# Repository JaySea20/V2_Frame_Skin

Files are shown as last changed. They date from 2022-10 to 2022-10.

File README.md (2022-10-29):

# V2_Frame_Skin  
Rounded Extrusion Covers to give your Voron 2.4 a sleek, smooth asthetic.  
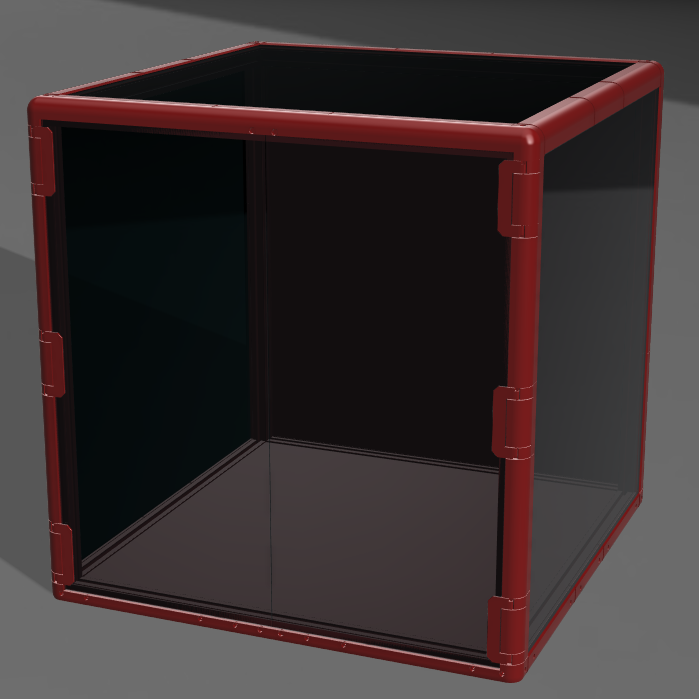
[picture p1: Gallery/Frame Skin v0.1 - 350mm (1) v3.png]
  
  
I Love my Voron 2.4r2. It sets a new bar for what a 3D Printer should be capable of.  
But, Ive never really liked the look of the Aluminum Extrusions that have been so commonly utilized for DIY CNC machines, printers, etc...  
And the only alternative seems to be the overly bulky quarter round extrusions like used in the DOOM project.  
So, I started from scratch with a few goals:  
 1 - As Low Profile as Possible. I have a 350 v2. I dont need that sucker being any bigger than it has to be ( or already is )  
 2 - Get rid of ALL sharp edges/corners/protrusions. Soon after I completed my build, I was walking past my newly built additive manufacturing beast of a printer and veered a bit too close. A corner caught just above my hip and left a nasty cut. Don't want to do that again.  
 3 - Must work with existing build. I didnt want to have to start swapping out extrusions, acrylic panels, or even have to disasemble anything gantry or below.  
 4 - As few visible screw heads as possible without overly complicating the installation.  
 5 - And, of course, it has to be a "printable" mod. ( All parts are printable besides a few screws and t-nuts. )  
   
 PLEASE NOTE:  
 These parts are not necessarily easy to print.  
 I found that printing them standing vertically worked the best for me. YMMV  
 Tolerances are tight. So calibration needs to be spot on. I tried printing some of them on my Ender3 and found its kinematics to be too sloppy.  
 Several of the parts will need supports. ( Hinge Body, Upper Corners, etc )  
   
 BOM  
| Part  | Quantity |
| --- | --- |
| Heat Set Inserts  | 4 |
| 6x3 Magnets | 8 |
| M3 Hammerhead T-Nuts| 32 |
| M3x12 SHCS | 4 |
| M3x8 SHCS | 32 |
| M2x16 SHCS | 12 |  
  
-Jay

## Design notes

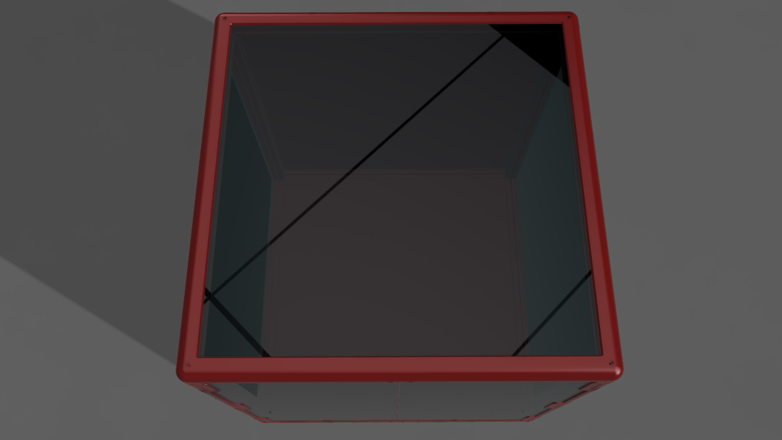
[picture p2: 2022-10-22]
Gallery/Frame Skin v0.1 - 350mm Top_view_front_profile.png

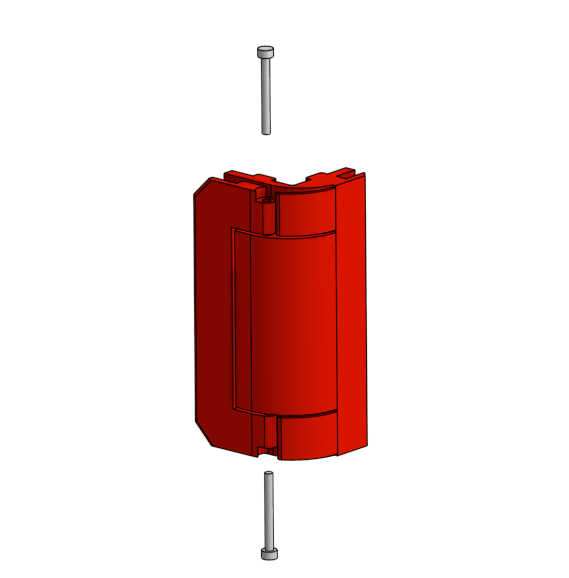
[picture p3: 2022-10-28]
Gallery/Hinge_Pins.png

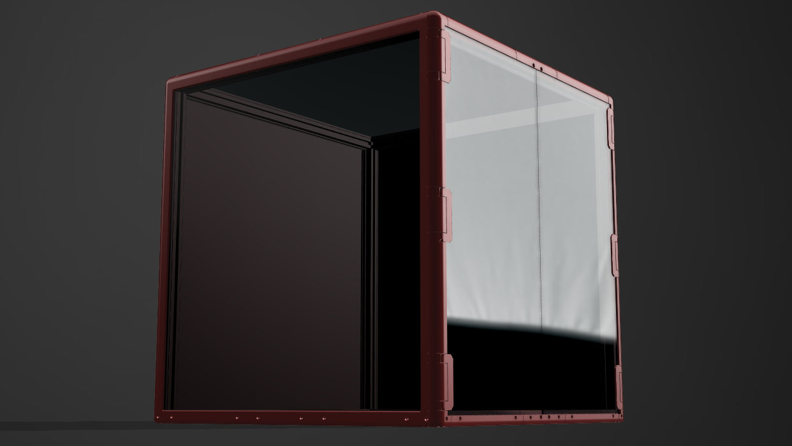
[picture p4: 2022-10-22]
Gallery/Frame Skin v0.1 - 350mm - Left_full_upwards.png

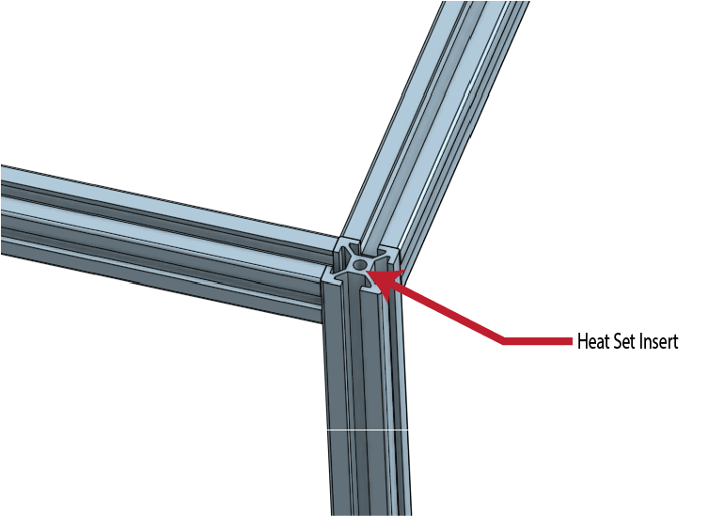
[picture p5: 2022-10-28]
Gallery/HeatSetInsert-01.png

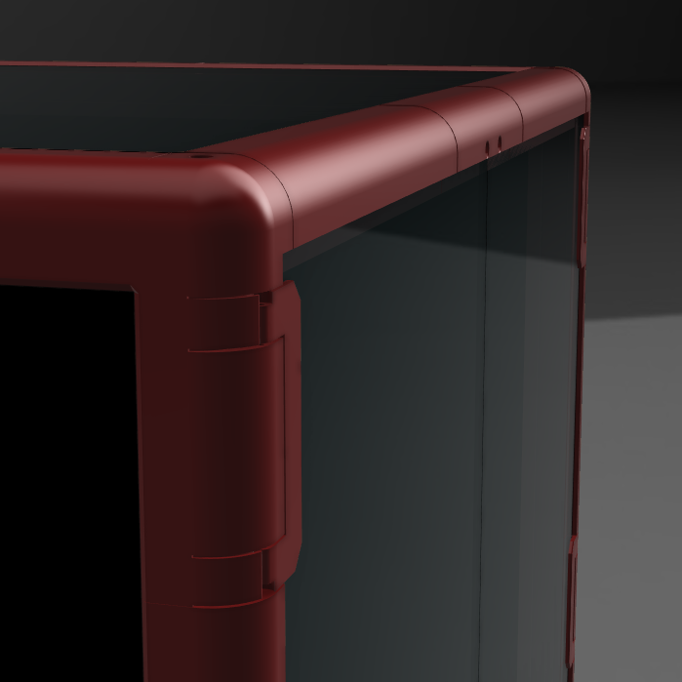
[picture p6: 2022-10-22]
Gallery/Frame Skin v0.1 - 350mm Zoomed_top_corner.png

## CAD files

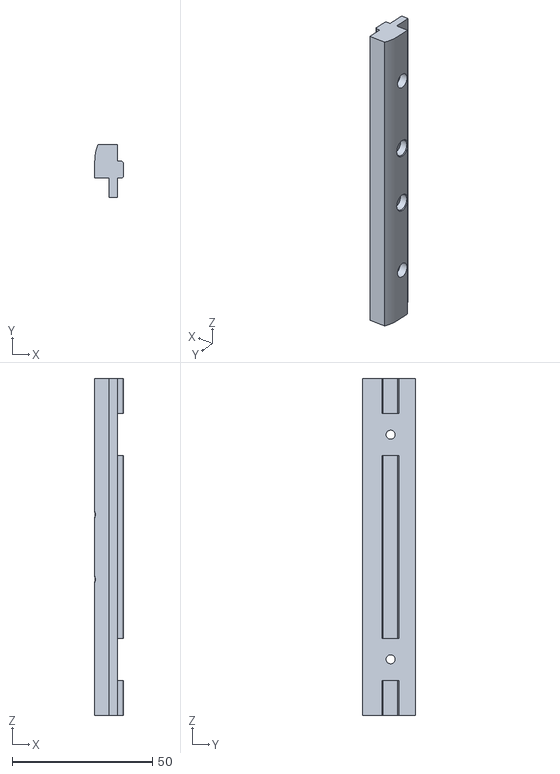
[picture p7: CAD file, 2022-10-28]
STL/350mm/Bottom_Front_Center_350_x1.stl
10.1 x 18.9 x 120.0

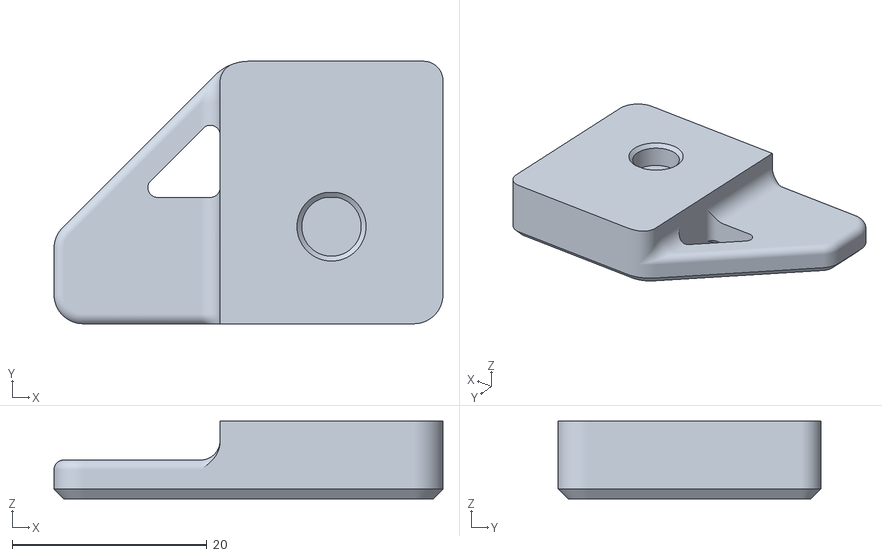
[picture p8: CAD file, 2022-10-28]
STL/Door_Handle_B_x2.stl
40.0 x 27.0 x 8.00

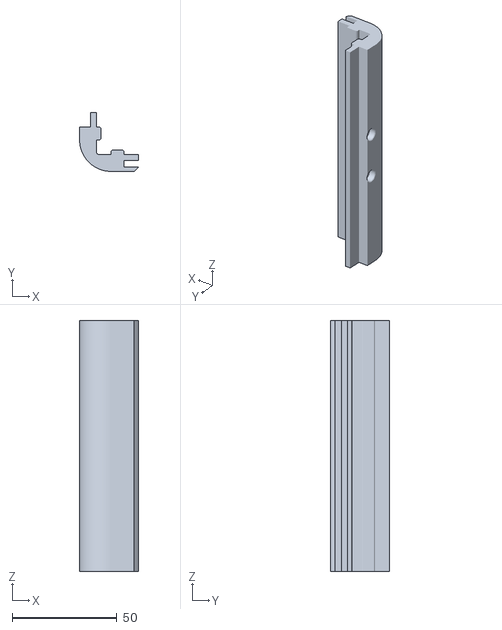
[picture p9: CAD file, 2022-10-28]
STL/350mm/Top_Front_Center_350_x1.stl
28.1 x 28.1 x 120.0

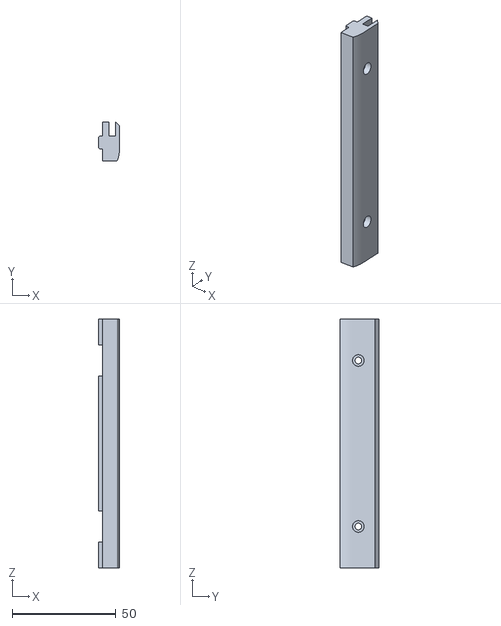
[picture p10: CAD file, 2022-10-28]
STL/350mm/Lower_120mm_350_x3.stl
10.2 x 18.9 x 120.0

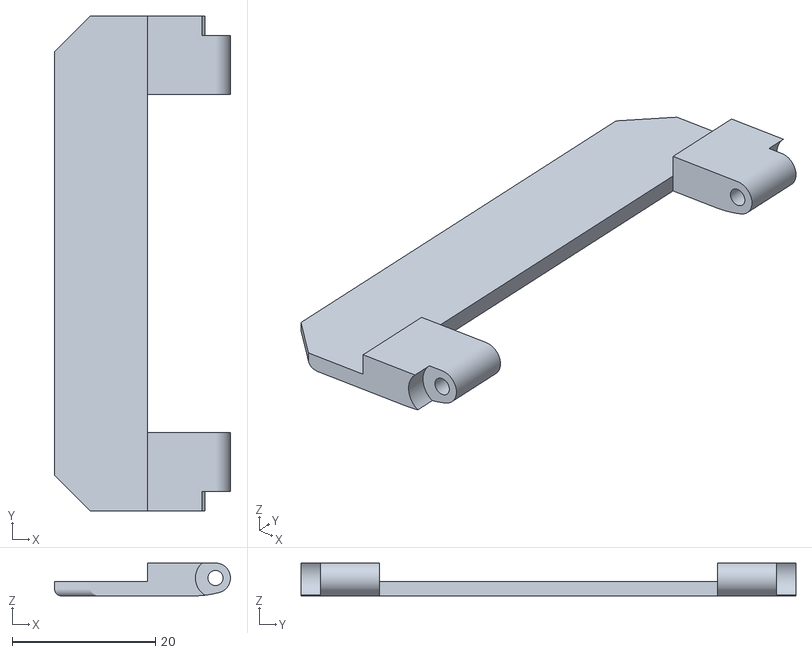
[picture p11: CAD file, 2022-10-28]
STL/Hinge_Arm_x6.stl
24.5 x 69.0 x 4.60

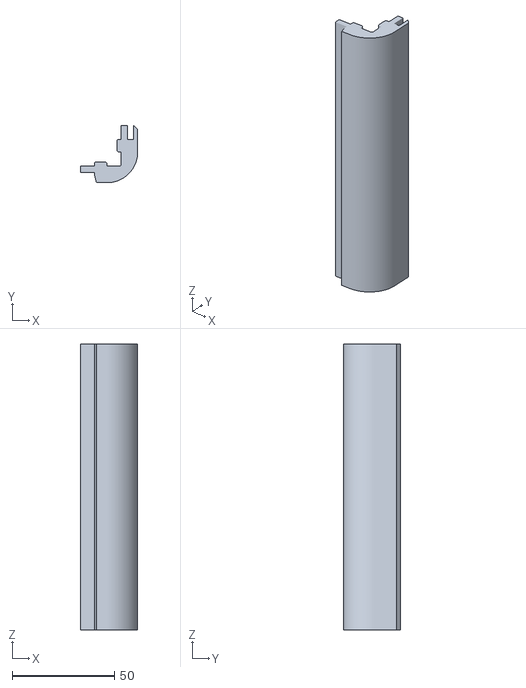
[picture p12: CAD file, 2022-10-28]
STL/350mm/Hinge_Spacer_140mm_350_x4.stl
28.1 x 28.1 x 140.0

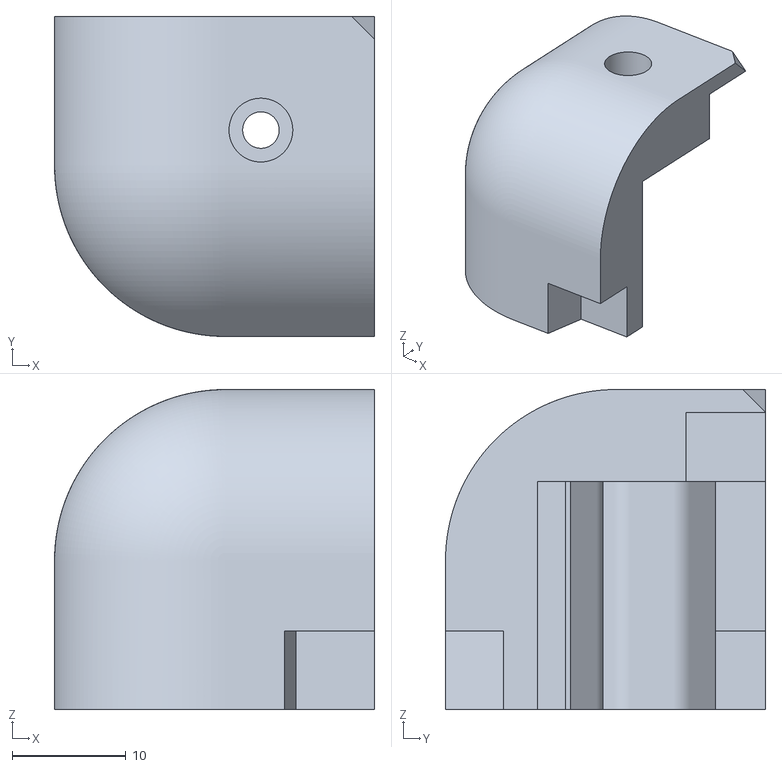
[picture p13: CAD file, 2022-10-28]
STL/Top_Front_Corner_L_x1.stl
28.1 x 28.1 x 28.1

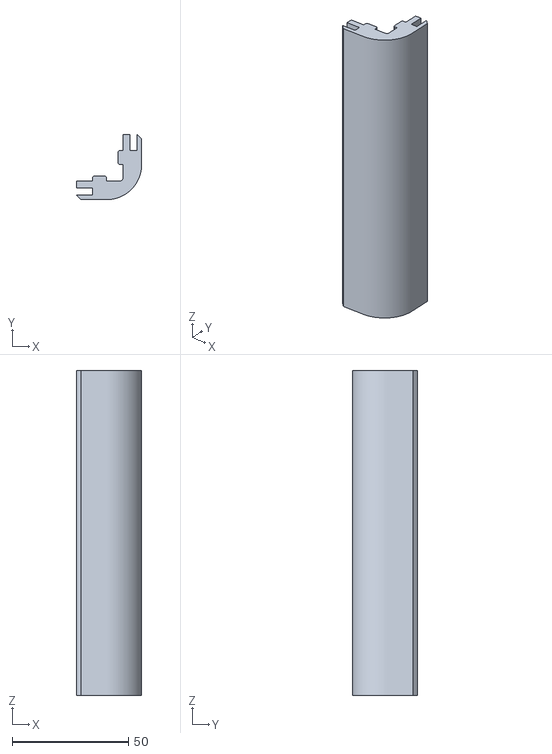
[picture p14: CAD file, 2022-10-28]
STL/350mm/Generic_140mm_350_x2.stl
28.1 x 28.1 x 140.0

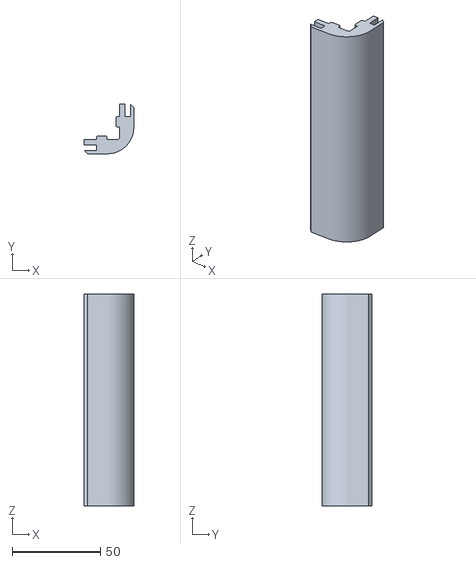
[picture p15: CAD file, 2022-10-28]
STL/350mm/Upper_120mm_350_x3.stl
28.1 x 28.1 x 120.0

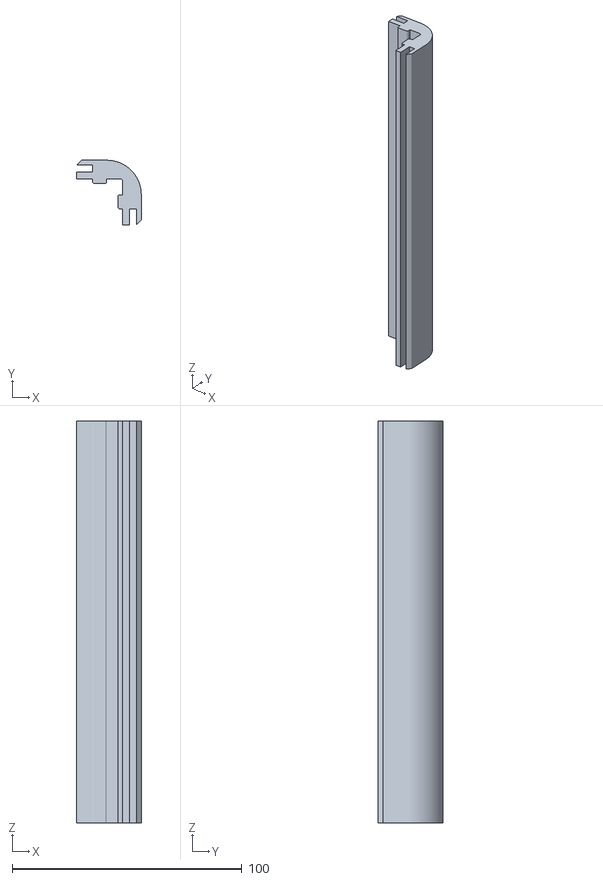
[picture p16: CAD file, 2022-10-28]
STL/Generic_175mm_x10.stl
28.1 x 28.1 x 175.0

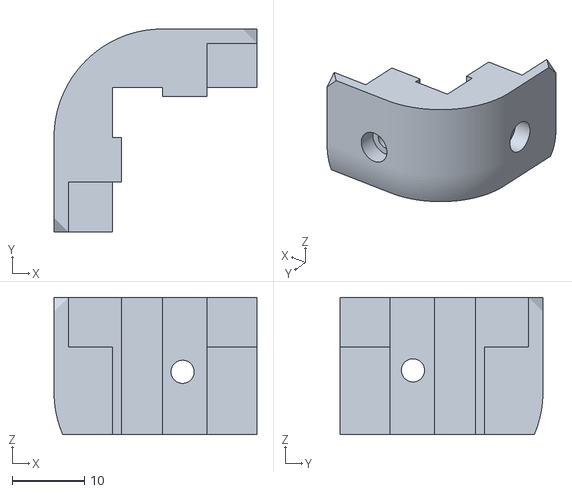
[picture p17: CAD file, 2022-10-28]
STL/Bottom_Back_Corner_x2.stl
28.1 x 28.1 x 19.0

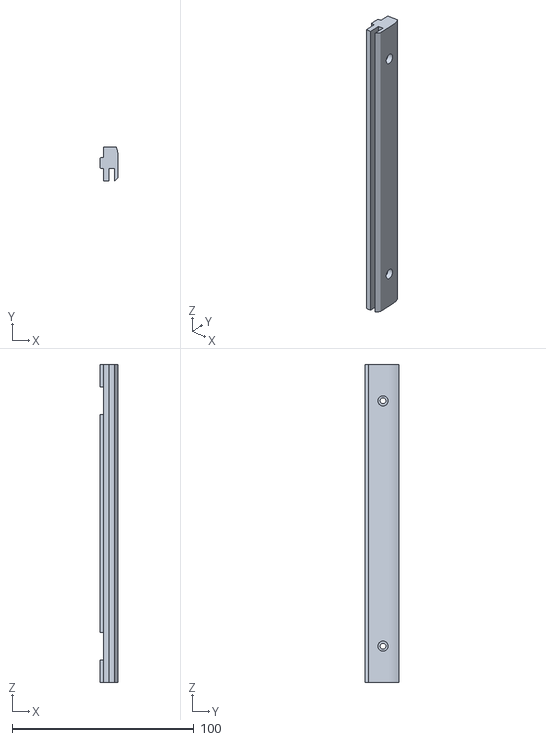
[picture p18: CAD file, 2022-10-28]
STL/Lower_175mm_x6.stl
10.2 x 19.0 x 175.0

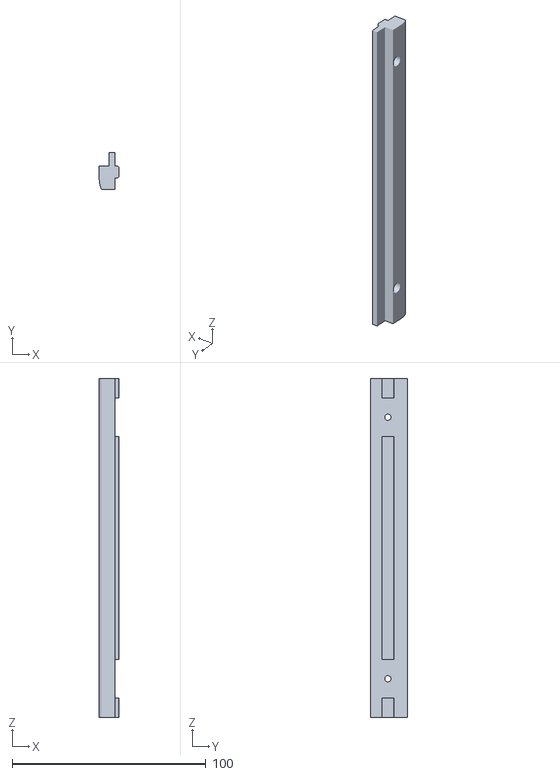
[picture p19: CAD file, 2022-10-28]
STL/Bottom_Front_175mm_x2.stl
10.1 x 18.9 x 175.0

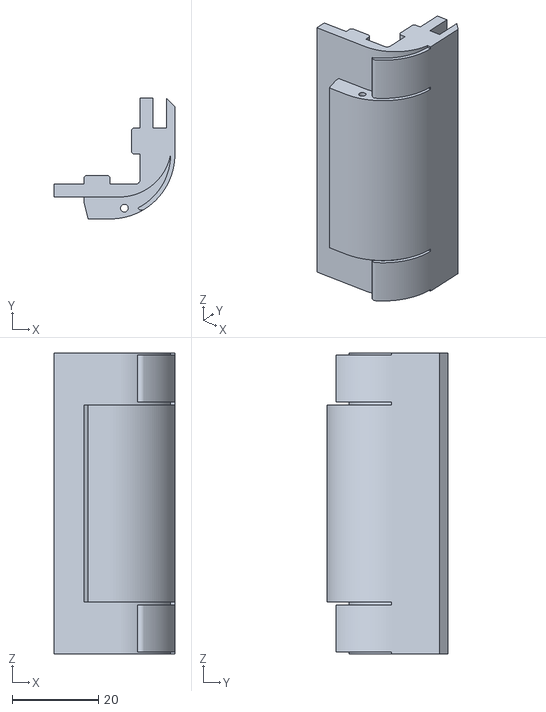
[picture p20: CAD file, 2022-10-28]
STL/Hinge_Body_x6.stl
28.1 x 28.1 x 70.0

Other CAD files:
STL/Door_Handle_A_x2.stl
STL/Top_Front_Corner_R_x1.stl
STL/Bottom_Front_Corner_R_x1.stl
STL/Bottom_Front_Corner_L_x1.stl
CAD/Frame_Skin_v010_350mm_CAD.f3d
STL/Top_Back_Corner_x2.stl
STL/Top_Front_175mm_x2.stl

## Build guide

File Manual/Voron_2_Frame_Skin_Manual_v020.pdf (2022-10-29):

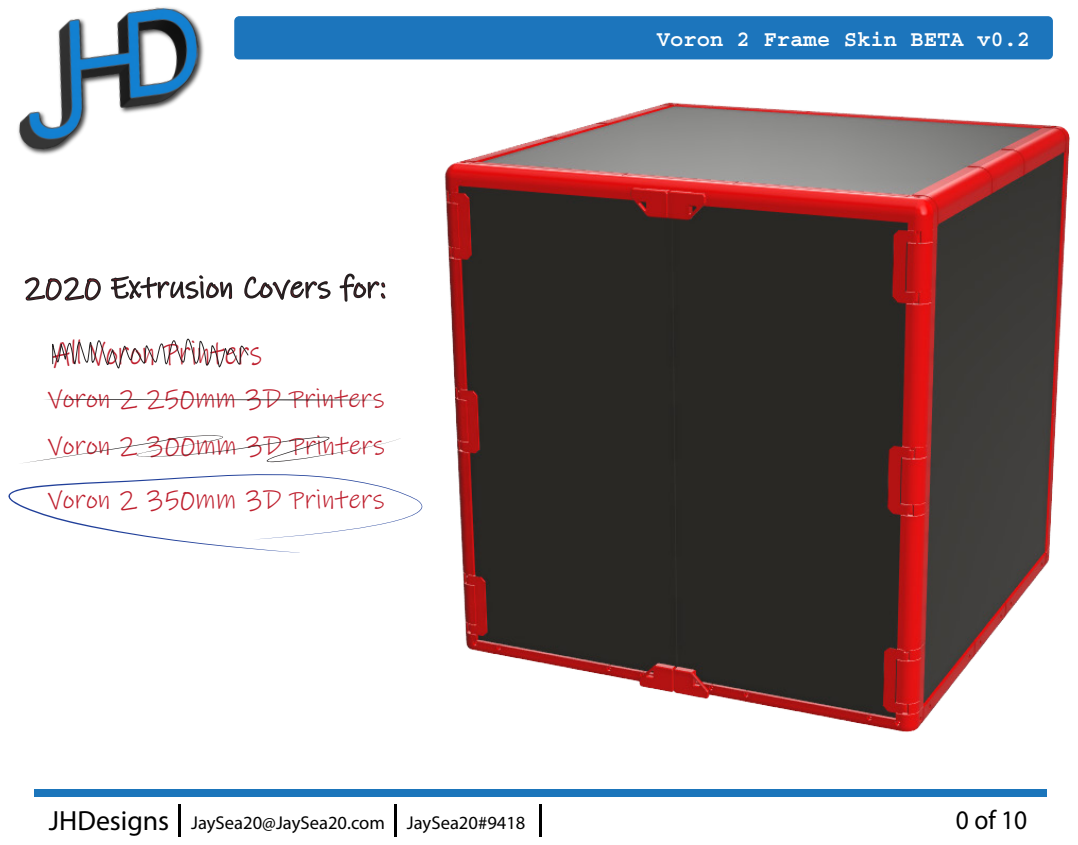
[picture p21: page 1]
JHDesigns; JaySea20@JaySea20.com; JaySea20#9418

Voron 2 Frame Skin BETA v0.2

2020 Extrusion Covers for:
All Voron Printers
Voron 2 250mm 3D Printers
Voron 2 300mm 3D Printers
Voron 2 350mm 3D Printers

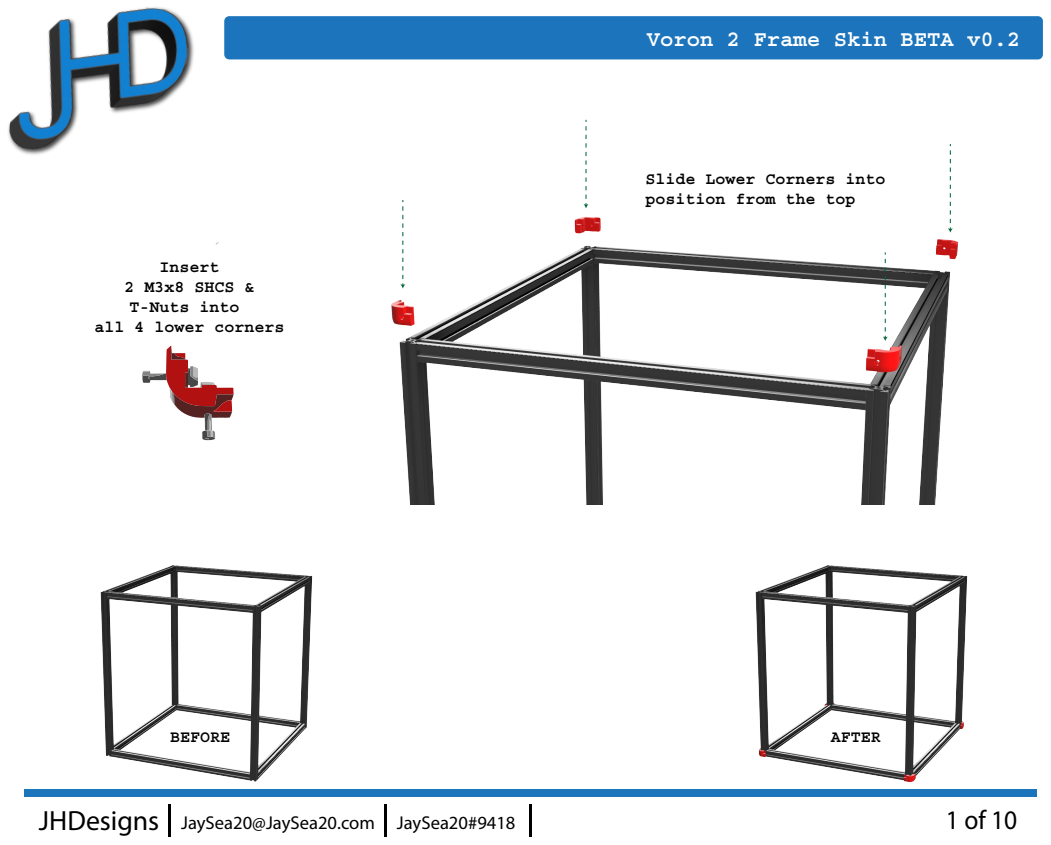
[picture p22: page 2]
JHDesigns; JaySea20@JaySea20.com; JaySea20#9418; BEFORE; AFTER

Slide Lower Corners into
position from the top

Insert
2 M3x8 SHCS &
T-Nuts into
all 4 lower corners

Add the rest of the lower section with M3x8 SHCS & T-Nuts in the same fashion

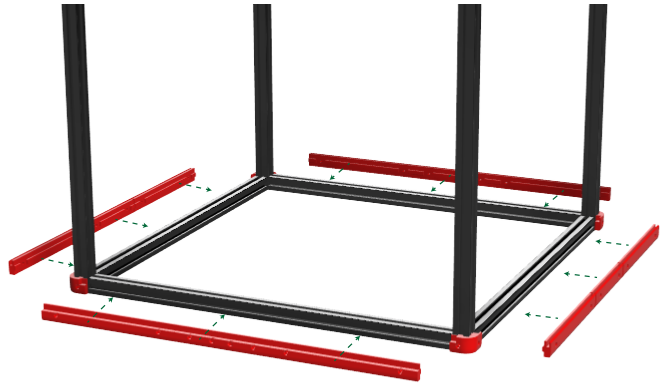
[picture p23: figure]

BEFORE | AFTER

Fasten Hinge Arm to
hinge body with
(2) M2x16 SHCS

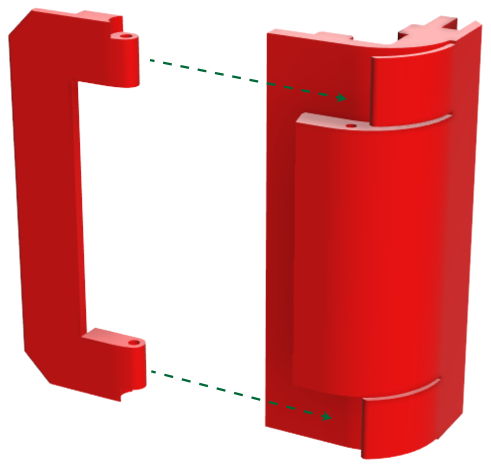
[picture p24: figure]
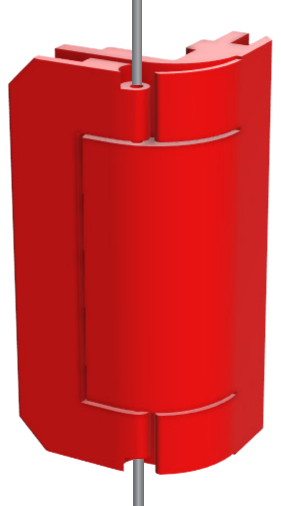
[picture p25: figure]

Repeat Process with
remaining hinges
(6) Total

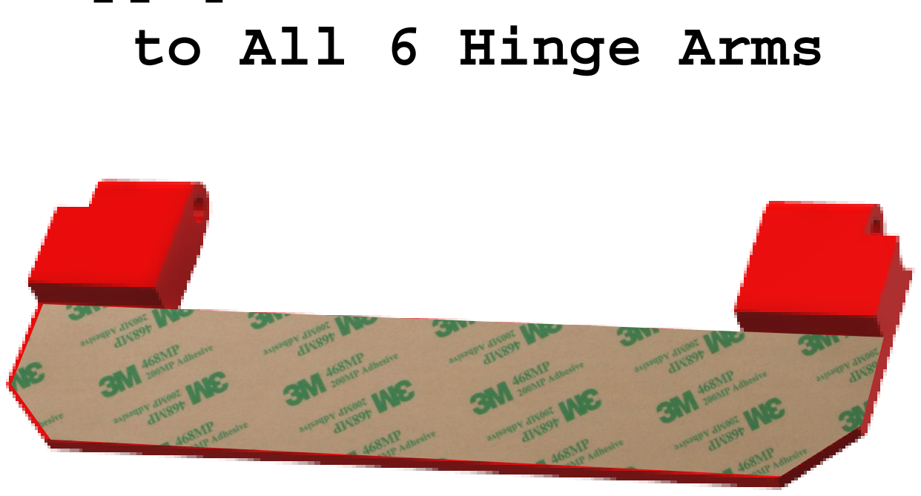
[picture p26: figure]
to All 6 Hinge Arms

Apply 3M 468MP Adhesive

NOTE: While it may be messy, silicone or other viscous glue would work.

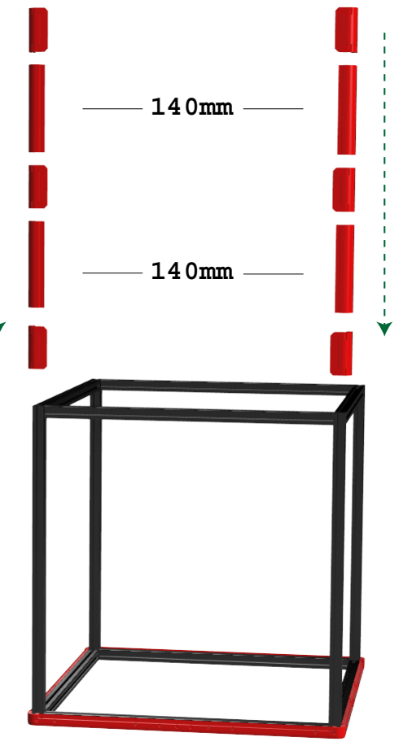
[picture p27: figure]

Slide Completed Hinges
& 140mm Sections onto
The front extrusions.
BEFORE | AFTER

Front Section

Rear Section

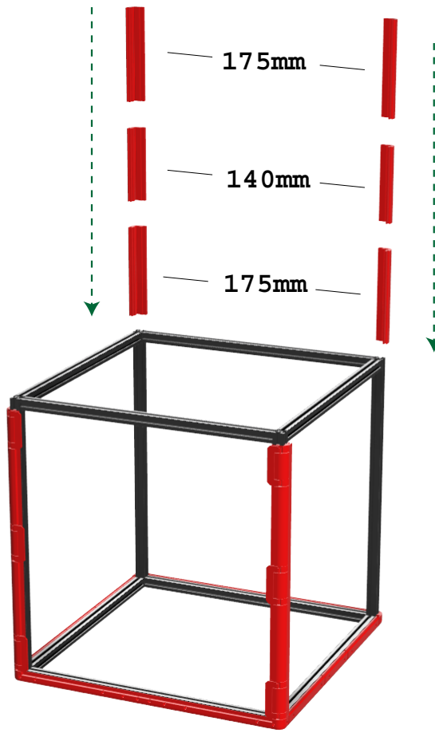
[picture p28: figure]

Slide Rear Sections
onto extrusions
BEFORE | AFTER

Front Section

Rear Section

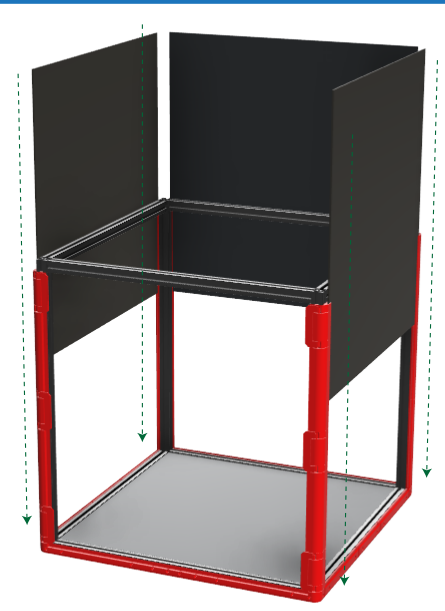
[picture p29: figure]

BEFORE | AFTER

Slide in Side & Rear
Acrylic Panels

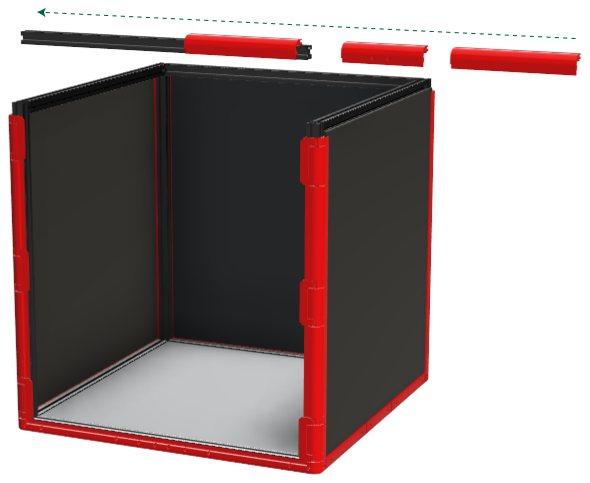
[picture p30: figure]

BEFORE | AFTER

Remove Upper Frame Sections one at a time and slide
the remaining sections
into place.

NOTE: Don’t forget to slide in the top panel before
completing the final side.

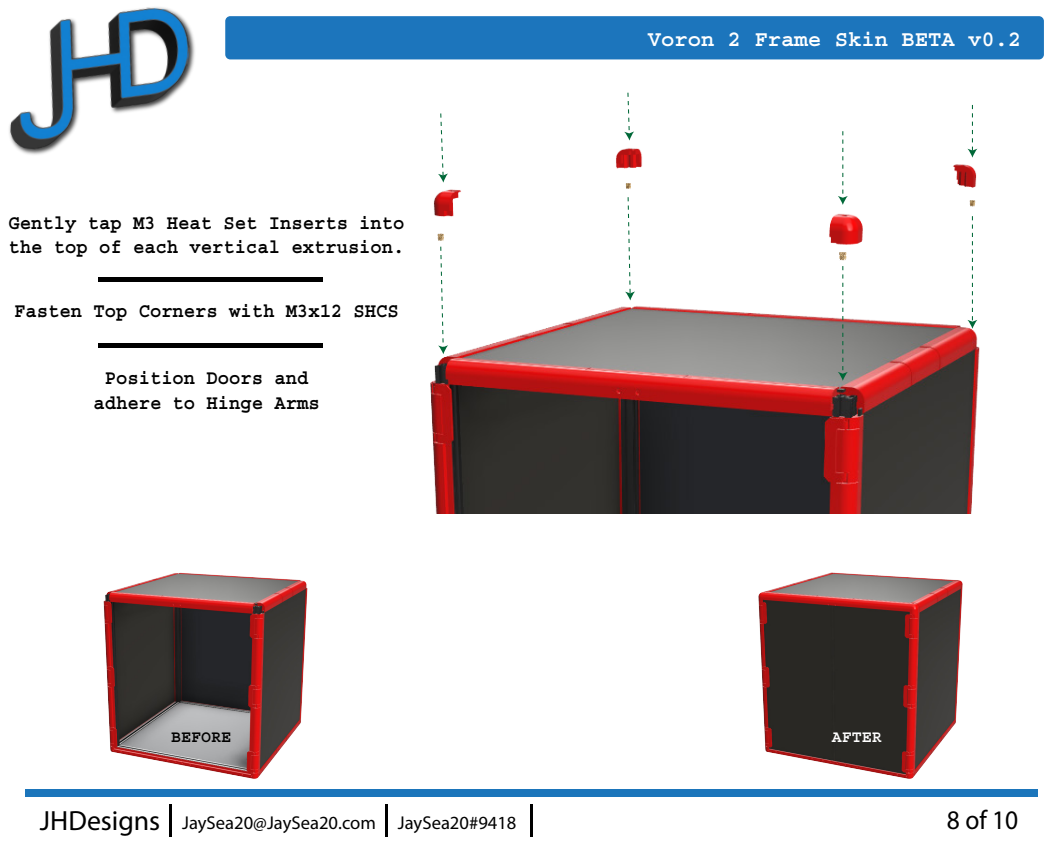
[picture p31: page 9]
BEFORE; AFTER

Gently tap M3 Heat Set Inserts into
the top of each vertical extrusion.

Fasten Top Corners with M3x12 SHCS

Position Doors and
adhere to Hinge Arms

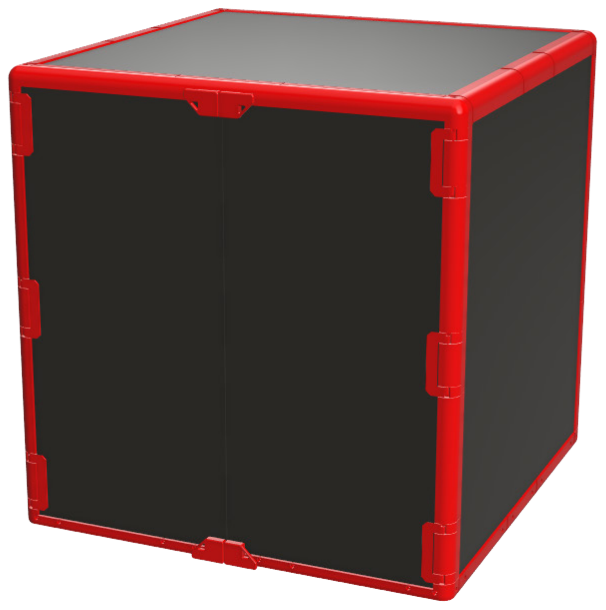
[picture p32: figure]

Add Magnets & Door Handles
